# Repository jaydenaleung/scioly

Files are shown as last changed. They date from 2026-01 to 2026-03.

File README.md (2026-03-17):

# 2026 Science Olympiad Electric Vehicle
## 10th Place at State Competition

This is my partner's and my electric vehicle for the Science Olympiad at Harvard SciOly and States SciOly. The Harvard version is a Front Wheel Drive, straight-line robot using a goBILDA Super Speed Servo to drive it. The attempted States version uses two wheels driven by two Super Speed Servos in addition to motor encoders for the velocity PID and the goBILDA Odometry setup for the position PID.

Screenshot 2026-03-16 at 7 50 26 PM

Screenshot 2026-03-16 at 7 50 26 PM

Screenshot 2026-03-16 at 7 50 26 PM

---

## How to Use

Harvard version: To use this vehicle, align the starting wheels with the long edge of the starting tape using the included alignment tool. Before removing the alignment tool, ensure that the micro limit switch is positioned directly behind the bumper at the back (i.e. it will not activate right when you start the robot). Remove the alignment tool and use a #2 pencil to click the button on the breadboard to start the vehicle.

States version: This version is unfinished and untested, but ideally, you'd use a measuring tool to angle the robot at a starting heading. **The starting position and heading are really important - any errors in these will offset the rest of the run.** Press the button and the robot should start.

## Why I Made This

Since I was a kid, I've always loved engineering, coding, and building things with my hands. As I've got more into building electronics, I wanted to try my hand at this build event for this year's Science Olympiad season. This robot is for my third SciOly season, and I wanted to spend time to build something custom and good this year.

Harvard:

Screenshot 2026-03-16 at 7 50 26 PM

States:

Screenshot 2026-03-16 at 7 50 26 PM

## 3D CAD Model

I used Onshape to design this electric vehicle. You can find the Onshape design at this [link](https://cad.onshape.com/documents/1f13c2afbaef7ea2c9c90426/w/eae7389462c6562ac928b722/e/d476c01702c9b15c2478fb6e), with a versioned history of Harvard and States iterations. All my CAD files are in the 'cad' folder.

Harvard:

Screenshot 2026-03-16 at 7 52 25 PM

States:

Screenshot 2026-03-16 at 7 50 26 PM

## Wiring

This robot does not use a PCB and uses jumper wires + a breadboard for its wiring. The wiring schematic is below:

Harvard:

Screenshot 2026-03-16 at 7 53 42 PM

Screenshot 2026-03-16 at 8 07 13 PM

## Programming

This robot should be programmed through the Arduino IDE as it uses an Arduino Uno. Please install the library in the 'firmware/libraries' folder into the Arduino IDE (instructions can be found online). **Do not install the goBILDA Pinpoint library typically found in the Arduino library search, as that is not compatible with the Arduino Uno. Use the included library in the firmware/libraries folder instead.**

## Bill of Materials (BOM) for V1 (Harvard)

| **Name** | **Quantity** | **Price (per part)** | **Link** |
| --- | --- | --- | --- |
| 90mm REV Traction Wheel | 4 | $6.25 | [https://www.revrobotics.com/DUO-Traction-Wheels/](https://www.revrobotics.com/DUO-Traction-Wheels/) |
| 30T 5mm Plastic Bore REV Gear | 1 | $1.25 | [https://www.revrobotics.com/5mm-Plastic-Hex-Bore-Gears/](https://www.revrobotics.com/5mm-Plastic-Hex-Bore-Gears/) |
| 30T goBILDA Brass Servo Gear | 1 | $10.99 | [https://www.gobilda.com/2305-series-brass-mod-0-8-servo-gear-25-tooth-spline-30-tooth/](https://www.gobilda.com/2305-series-brass-mod-0-8-servo-gear-25-tooth-spline-30-tooth/) |
| 135mm (Length) 5mm (Width) REV Hex Shaft | 2 | $4.38 | [https://www.revrobotics.com/5mm-Hex-Shafts/](https://www.revrobotics.com/5mm-Hex-Shafts/) |
| REV Long Through Bore Bearing | 4 | $0.65 | [https://www.revrobotics.com/Through-Bore-Bearings/](https://www.revrobotics.com/Through-Bore-Bearings/) |
| REV Shaft Collar | 4 | $0.975 | [https://www.revrobotics.com/rev-41-1327-pk10/](https://www.revrobotics.com/rev-41-1327-pk10/) |
| HiLetgo Micro Limit Switch KW12-3 | 1 | $0.60 | [https://www.amazon.com/HiLetgo-KW12-3-Roller-Switch-Normally/dp/B07X142VGC](https://www.amazon.com/HiLetgo-KW12-3-Roller-Switch-Normally/dp/B07X142VGC) |
| REV 39mm Tensioning Bushing | 4 | $1.50 | [https://www.revrobotics.com/rev-41-1702/](https://www.revrobotics.com/rev-41-1702/) |
| goBILDA Super Speed Servo | 1 | $36.99 | [https://www.gobilda.com/2000-series-dual-mode-servo-25-4-super-speed/](https://www.gobilda.com/2000-series-dual-mode-servo-25-4-super-speed/) |
| Arduino Uno R3 | 1 | $14.99 | [https://www.amazon.com/ELEGOO-Board-ATmega328P-ATMEGA16U2-Compliant/dp/B01EWOE0UU/](https://www.amazon.com/ELEGOO-Board-ATmega328P-ATMEGA16U2-Compliant/dp/B01EWOE0UU/) |
| 9V Battery Cable | 1 | $0.50 | [https://www.amazon.com/Battery-Connector-Plastic-Experiment-Equipment/dp/B08SL9X2YC/](https://www.amazon.com/Battery-Connector-Plastic-Experiment-Equipment/dp/B08SL9X2YC/) |
| 9V Alkaline Battery | 1 | $1.59 | [https://www.amazon.com/Battery-Connector-Plastic-Experiment-Equipment/dp/B08SL9X2YC/](https://www.amazon.com/Battery-Connector-Plastic-Experiment-Equipment/dp/B08SL9X2YC/) |
| ¼” Wooden Dowel | 1 | $0.12 | [https://www.amazon.com/Dowel-Rods-Natural-Projects-Hardwood/dp/B0CR7J7YBJ/](https://www.amazon.com/Dowel-Rods-Natural-Projects-Hardwood/dp/B0CR7J7YBJ/) |
| **Total** | | | **$80.79** |

## Bill of Materials (BOM) for V2 (Attempted States)

| **Name** | **Quantity** | **Price (per part)** | **Link** |
| --- | --- | --- | --- |
| goBILDA 3607 Series Disc Wheel (14mm Bore, 120mm Diameter, Black) | 2 | $4.49 | [https://www.gobilda.com/3607-series-disc-wheel-14mm-bore-120mm-diameter-black-2-pack/](https://www.gobilda.com/4-bar-odometry-pack-2-pods-1-pinpoint-computer/) |
| goBILDA 4-Bar Odometry Pack (2 Pods, 1 Pinpoint Computer) | 1  | $279.99 | [https://www.gobilda.com/4-bar-odometry-pack-2-pods-1-pinpoint-computer/](https://www.gobilda.com/4-bar-odometry-pack-2-pods-1-pinpoint-computer/) |
| goBILDA 1309 Series Sonic Hub (8mm REX® Bore) | 4  | $7.99 | [https://www.gobilda.com/4-bar-odometry-pack-2-pods-1-pinpoint-computer/\](https://www.gobilda.com/4-bar-odometry-pack-2-pods-1-pinpoint-computer/](<https://www.gobilda.com/4-bar-odometry-pack-2-pods-1-pinpoint-computer/\](https://www.gobilda.com/4-bar-odometry-pack-2-pods-1-pinpoint-computer/>) |
| goBILDA 8mm REX® Shaft with E-Clip (Stainless Steel, 40mm Length) | 2  | $4.09 | [https://www.gobilda.com/8mm-rex-shaft-with-e-clip-stainless-steel-40mm-length/](https://www.gobilda.com/8mm-rex-shaft-with-e-clip-stainless-steel-40mm-length/) |
| M4 Nuts and Bolts | 29 (# of bolts, buy an equal amount of nuts)  | $0.03 | [https://www.amazon.com/VGBUY-312Pcs-Screws-25-50mm-Assortment/dp/B0DD7D6VP5/](https://www.amazon.com/VGBUY-312Pcs-Screws-25-50mm-Assortment/dp/B0DD7D6VP5/) |
| M3 Nuts and Bolts | 4 (# of bolts, buy an equal amount of nuts)  | $0.02 | [https://www.amazon.com/VGBUY-312Pcs-Screws-25-50mm-Assortment/dp/B0D14BC8QS/](https://www.amazon.com/VGBUY-312Pcs-Screws-25-50mm-Assortment/dp/B0D14BC8QS/) |
| Arduino Uno R3 | 1 | $14.99 | [https://www.amazon.com/ELEGOO-Board-ATmega328P-ATMEGA16U2-Compliant/dp/B01EWOE0UU/](https://www.amazon.com/ELEGOO-Board-ATmega328P-ATMEGA16U2-Compliant/dp/B01EWOE0UU/) |
| 30T goBILDA Brass Servo Gear | 1 | $10.99 | [https://www.gobilda.com/2305-series-brass-mod-0-8-servo-gear-25-tooth-spline-30-tooth/](https://www.gobilda.com/2305-series-brass-mod-0-8-servo-gear-25-tooth-spline-30-tooth/) |
| goBILDA Super Speed Servo | 2 | $36.99 | [https://www.gobilda.com/2000-series-dual-mode-servo-25-4-super-speed/](https://www.gobilda.com/2000-series-dual-mode-servo-25-4-super-speed/) |
| REV 39mm Tensioning Bushing | 4 | $1.50 | [https://www.revrobotics.com/rev-41-1702/](https://www.revrobotics.com/rev-41-1702/) |
| 18mmx9mm Bubble Level | 1 | $0.95 | [https://www.aliexpress.us/item/3256808611329580.html](https://www.aliexpress.us/item/3256808611329580.html) |
| Steel Caster Wheels | 1 | $2.50 | [https://www.amazon.com/dp/B0C69FYKC3/](https://www.amazon.com/dp/B0C69FYKC3/) |
| DC Motor Rotary Quadrature Encoder 600P/R | 2 | $18.99 | [https://www.amazon.com/dp/B07MX1SYXB/](https://www.amazon.com/dp/B07MX1SYXB/) |
| AA Battery Holder | 1 | $4.50 | [https://www.amazon.com/Thicken-Battery-Holder-Standard-Connector/dp/B07WP1CYYW/](https://www.amazon.com/Thicken-Battery-Holder-Standard-Connector/dp/B07WP1CYYW/) |
| AA NiMH Batteries | 8 | $1.60 | [https://www.amazon.com/AmazonBasics-Rechargeable-Batteries-8-Pack-Pre-charged/dp/B00CWNMV4G/](https://www.amazon.com/AmazonBasics-Rechargeable-Batteries-8-Pack-Pre-charged/dp/B00CWNMV4G/) |
| ¼” Wooden Dowel | 1 | $0.12 | [https://www.amazon.com/Dowel-Rods-Natural-Projects-Hardwood/dp/B0CR7J7YBJ/](https://www.amazon.com/Dowel-Rods-Natural-Projects-Hardwood/dp/B0CR7J7YBJ/) |
| **Total** | | | **$476.83** |

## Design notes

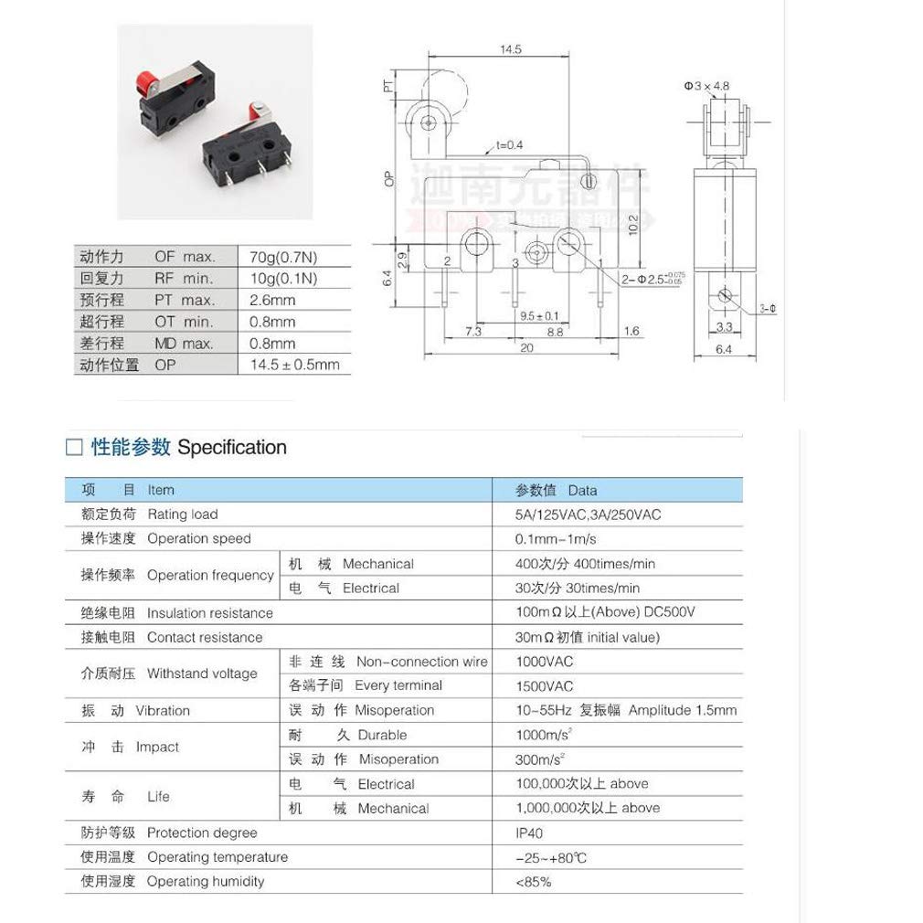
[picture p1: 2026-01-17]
cad/refs/micro-limit-switch-datasheet.jpg

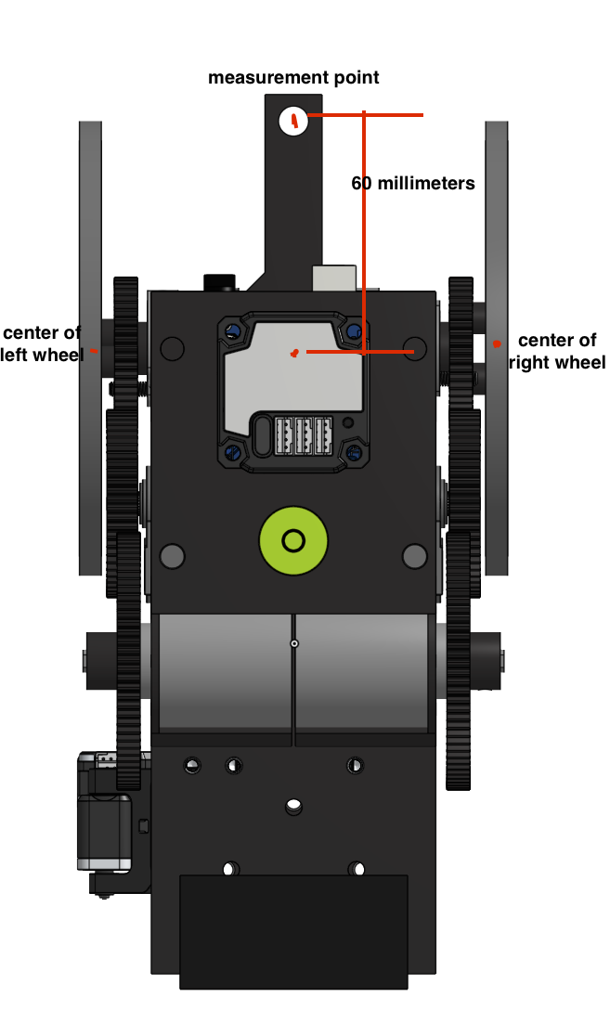
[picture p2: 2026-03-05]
cad/refs/f7532c4e-d770-4caa-af58-1f401a9bbd4f.png

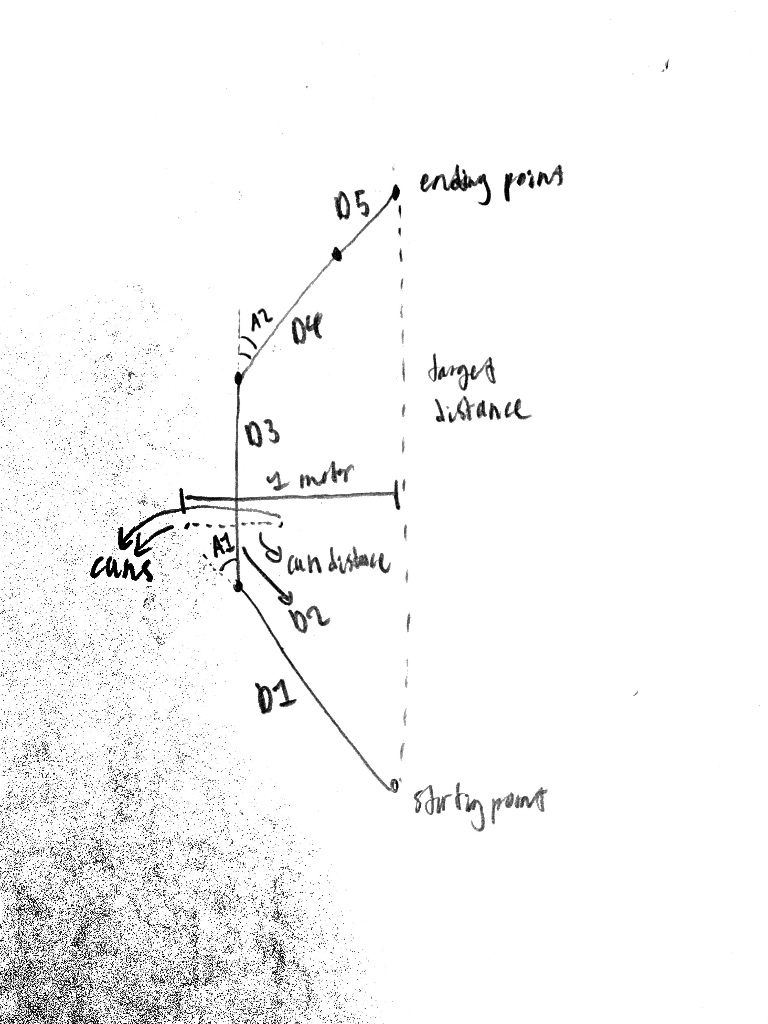
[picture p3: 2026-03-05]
cad/refs/8a76730c-c149-4180-b7a8-759c86ef1397.jpg

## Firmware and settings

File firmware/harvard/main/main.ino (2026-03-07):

#include "Servo.h"

// Connections
Servo s;

const int buttonPin = 7;
const int switchPin = 8;
const int servoPin = 9;

// Measurements
const double diameter = 9.0; // average diameter of BACK wheels in cm
const double circumference = PI*diameter;

////// COMP PARAMS //////
const double TARGET_DIST = 870.0; // in cm
const double TARGET_REVS = TARGET_DIST / circumference;
const int TARGET_REVS_FLOOR = (int)TARGET_REVS;
const int TARGET_CLICKS = TARGET_REVS_FLOOR * 4;

const double TARGET_TIME = 12.5; // in s
const double TARGET_TIME_MS = TARGET_TIME*1000.0; // in ms

// Speed logic
const int maxServoSpeed = 0; // fastest the servo can run without the limit switch skipping revs
const double maxEndRealSpeed = 43.62688; // see spreadsheet & journal to see how I got this
const int maxEndServoSpeed = 72;

double dist = 0.0; // current distance from start line
double currentFinalEndDist = 0.0; // recording distance from the last press of the switch

const int endRevs = 3; // # of revs before end line to stop rolling, excluding any partial revs because TARGET_DIST does not divide with revs as a whole
const double bufferDist = endRevs * circumference; // distance from the beginning of the "buffer" revs to the last "buffer" rev - e.g. if endRevs = 1, then bufferDist = circumference, if eR = 2, bD = 2*circ, etc.
const double finalDist = (TARGET_REVS - TARGET_REVS_FLOOR) * circumference; // distance from last rev to end
const double endDist = bufferDist + finalDist; // how much dist is left before the end - endRevs revs + the rest

double endTime; // how much time is left before the end
double endRealSpeed; // calculated later with endDist/Time
double endServoSpeed; // this is what you put in

int currentSpeed = -1; // current speed

// Button properties & debounce
int clicks = 0;
double revs = 0.0; // how many revs you've GONE

int clicksPerRev = 4;

int lastButtonState = HIGH;
int lastSwitchState = HIGH;

int currentButtonState;
int currentSwitchState = HIGH; // default not pressed

unsigned long lastDebounceTime = 0;
const int debounceDelay = 5; // for limitswitch

// Flags
bool start = false;
bool triggerSlow = false;
bool slow = false;
bool triggerFinal = false;
bool calculateFinalEndDist = false;
bool end = false;

// Timing
double t; // in ms
double finalEndT; // millis() time at the start of the final period
double endElapsedTime;
double currentTime;
bool startTiming = false;
void updateTime() { currentTime = millis() - t; }


void setup() {
    Serial.begin(9600);
    Serial.println("Setup started");

    // Connections
    s.attach(servoPin);
    pinMode(buttonPin, INPUT_PULLUP);
    pinMode(switchPin, INPUT_PULLUP);
}

void loop() {
    // Start button
    currentButtonState = digitalRead(buttonPin);
    if (!start && currentButtonState == LOW && lastButtonState == HIGH) { // LOW = pressed, HIGH = not pressed
        Serial.println("button started");
        start = true;
        startTiming = true;
    }
    lastButtonState = currentButtonState;
    
    // Main logic
    if (start) {
        // Initial commands after starting
        if (startTiming) {
            t = millis();

            currentSpeed = -maxServoSpeed;
            s.write(-maxServoSpeed); // negative for the right direction

            startTiming = false;
        }

        // Time update
        if (!end) {
            updateTime();
        }

        // Serial print time exceeded
        if (!end && currentTime >= TARGET_TIME_MS) { // If TARGET_TIME_MS exceeded
            Serial.println("TIME EXCEEDED BY: " + String((millis()-t-TARGET_TIME_MS)/1000.0) + " s");
        }

        // Limit switch
        int switchReading = digitalRead(switchPin); // temporary reading that will be assigned to currentSwitchState if confirmed
        if (switchReading != lastSwitchState) { lastDebounceTime = millis(); } // start debounce timer
        if ((millis() - lastDebounceTime) > debounceDelay) { // signal cleared debounce delay
            if (switchReading != currentSwitchState) { // confirm debounce
                currentSwitchState = switchReading;
                if (!calculateFinalEndDist && currentSwitchState == LOW) { // confirm LOW
                    clicks++;
                    revs = (double)clicks/clicksPerRev;
                    dist = revs*circumference; // recalculate
                    Serial.println("revs = " + String(revs));
                }
            }
        }
        lastSwitchState = switchReading;

        // Beginning of slow period / slow period trigger
        if (revs == TARGET_REVS_FLOOR - endRevs && !triggerSlow) {
            // Trigger flag to compute end parameters and slow down
            slow = true;
            triggerSlow = true;
        }

        // Slow period logic
        if (slow) {
            // Compute endTime, endSpeed
            endTime = (TARGET_TIME_MS - currentTime)/1000.0; // in s

            if (currentTime < TARGET_TIME_MS && abs(endTime) > endDist/maxEndRealSpeed) { // if the car has not passed the target time AND has adequate time to cross (meaning there is more time than the time it would take to run at maxEndSpeed)
                endRealSpeed = endDist/endTime;
                Serial.println(endRealSpeed);
                endServoSpeed = -0.389298 * endRealSpeed + 88.70013; // regression model from spreadsheet
            } else {
                // move at max possible reliable speed to get to finish line at endDist --> see journal and spreadsheet to see how I got this number
                endServoSpeed = maxEndServoSpeed;
                endRealSpeed = maxEndRealSpeed;
            }

            currentSpeed = endServoSpeed;
            s.write(endServoSpeed);
            Serial.println("current speed = " + String(currentSpeed));

            slow = false;
        }

        // Beginning of final period, i.e. period beginning after switch is hit for the last time / final period trigger
        if (clicks == TARGET_CLICKS && !triggerFinal) {
            // calculateFinalEndDist = true;
            // finalEndT = millis();
            end = true;
            triggerFinal = true;
        }

        // // Final period logic
        // if (calculateFinalEndDist) {
        //     endElapsedTime = millis() - finalEndT;
        //     currentFinalEndDist = endRealSpeed * (endElapsedTime / 1000.0); // also convert endElapsedTime to secs
        // }

        // Beginning of end period / end period trigger
        // if (currentFinalEndDist >= finalDist) {
        //     dist += currentFinalEndDist;
            
        //     calculateFinalEndDist = false;
        //     end = true;
        // }

        // End period logic - you're done!
        if (end) {
            currentSpeed = 90;
            s.write(90);

            // End stats
            Serial.println("Total distance covered: " + String(dist));
            Serial.println("Total time elapsed: " + String(currentTime));

            start = false;
        }
    }

    // Serial.println("current speed = " + String(currentSpeed));
    // Serial.println("revs = " + String(revs));
}

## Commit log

2026-01-09 code and pcb init
    [electric_vehicle_2026.kicad_pcb, electric_vehicle_2026.kicad_sch]
2026-01-18 Write full code and schematic
    [electric_vehicle_2026.kicad_sch]
2026-03-05 Replace main.ino with cascaded PID controller for Electric Vehicle
    - Cascaded PID: outer heading PID + two inner velocity PIDs (one per wheel)
    - goBILDA odometry via I2C for (x, y, heading) pose estimation
    - Measurement-point offset: (0, +60mm) from wheel-axle midpoint
    - Full track geometry computed from day-of TARGET_DIST and TARGET_TIME
    - 6-waypoint trapezoidal track with D1,D4,A1,A2 auto-computed
    - Gear train accounting: 60T servo, 45T wheel, 83T encoder
    - Quadrature encoder velocity measurement (600 PPR)
    - State machine: IDLE -> STRAIGHT -> TURNING -> FINAL_APPROACH -> DONE
    - Final approach strategy: slow to arrive exactly on time, or maintain speed
    - User-adjustable parameters: TARGET_D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
    [main.ino]
2026-03-05 Integrate goBILDA Pinpoint, Encoder, and PID_v1 Arduino libraries
    Replace custom implementations with standard Arduino libraries:
    1. goBILDA_Pinpoint.h (official goBILDA Pinpoint Odometry Computer library)
    - Replaces manual I2C register reads (odomRead16, ODOM_I2C_ADDR, etc.)
    - Uses pinpoint.getPosition() for fused (x, y, heading) pose data
    - Configured for goBILDA 4-bar odometry pods
    2. Encoder.h (Paul Stoffregen's quadrature encoder library)
    - Replaces volatile counters and manual ISR functions
    - Library handles interrupt setup and quadrature decoding internally
    - Uses encL.read() / encR.read() for thread-safe count retrieval
    3. PID_v1.h (Brett Beauregard's PID library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
    [main.ino]
2026-03-05 Add sample time justification comment for PID controllers
2026-03-05 add surface files
    [electric_vehicle_2026.kicad_pcb, electric_vehicle_2026.kicad_sch]
2026-03-06 pinpoint library fix and initial fixes to code
    [main.ino]
2026-03-07 Revert and tweak code for 4x clicks per rev
    [main.ino]
2026-03-16 reorganized structure
    [BOM.csv, electric_vehicle_2026.kicad_pcb, electric_vehicle_2026.kicad_sch]
2026-03-16 bom and readme
    [BOM-harvard.csv, BOM-states.csv]
2026-03-17 change schematic for states
    [electric_vehicle_2026.kicad_sch]
2026-03-17 Simplify programming instructions in README
    Removed redundant information about the robot's programming and PID tuning.
